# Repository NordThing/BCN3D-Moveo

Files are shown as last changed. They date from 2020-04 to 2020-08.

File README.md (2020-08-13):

## NordThing - What we want to achieve
Make the robotic - and after that try to improve the overall part-list. Now it´s a lot of sourcing of different parts.
It would be nice to minimize the different kind of screws needed.

#What we have modified below this line

Changes:
We have put up a new folder for a Product Breakdown Structure - where it´s easy to see what parts needed and in which phase the project are in right now. This is also possible to modify if we want to 3d print parts or maybe CNC-parts.

#BOM 

Added a file that are changeable and also a progress file for me us as we continue our project

#CAD

We have added a Fusion360 design.

#STL

Put the right orientation of the part to print and also included if support is needed or not.
New parts marked as Nordthing in the end of the files - the original files is still in the folder - with the original name.

Added a picture to ever part that is printed.

## BCN3D MOVEO - ORIGINAL BELOW THIS LINE

This is the repository that contains the CAD files, the STL files, the user manual (with the assembly manual), the firmware, and the Bill of Materials of the BCN3D Moveo.
BCN3D Technologies keeps taking important steps in order to achieve his goal of bringing the digital manufacturing technology to everyone. In this occasion we are presenting the BCN3D Moveo, a robotic arm design from scratch and developed by our engineers in collaboration with the Departament d’Ensenyament from the Generalitat de Catalunya. Its structure is fully printed using additive manufacturing technologies and its electronics are controlled by the software Arduino.
Moveo, fully functional nowadays, has been born, as all the BCN3D Technologies products, with an open and educational wish.

##Why BCN3D Moveo

One of the Departament d’Ensenyament worries is the high price of the materials the grade students must use on their internships. Holding that in mind, an Open Source robotic arm, adaptable by the students and low cost reproducible could take several educational itineraries: mechanical design, automatism, industrial programing, etc.
Thus, the BCN3D Moveo should allow the educational centers to enjoy a modifiable and easily accessible for the students, at a price far lower than the usual industrial equipment they used to have to acquire, with enough output for training purposes.
As a Fundació CIM area, BCN3D Technologies shares its educational vocation. That is the reason why when the Departament d’Ensenyament contacted us in order to suggest and offer this project a year ago we didn’t hesitate on taking that opportunity.
Once we had the robotic arm designed and manufactured we started the last phase of the project, which consisted on an assembling and fine tuning workshop for 15 institutes around Catalonia, which took place in the BCN3D Technologies.
These institutes already have the BCN3D Moveo in their classrooms and workshops, and will have to present an internship program that proves their knowledge about the arm during September.

##Open Source Technology: Github

As we have done with all our developed produtcs, the BCN3D Moveo files will be available for everyone. Thanks to the platform Github, a website where users around the world share their designs, anyone will be able to obtain all the necessary information in order to assemble his own BCN3D Moveo at home.

Unlike the other BCN3D products, the Moveo won’t be commercialized. The project has been born and developed in order to make a move for the community progress starting from the Departament d’Ensenyament idea.
Nevertheless, BCN3D will fee all the Moveo know how on our Github account, as we have been doing with all the BCN3D Technologies products. Thus, the users will be able to find the bill of material (BOM), where all the needed components for the assembling of the arm come detailed, as the CAD designs, so anyone will be able to modify the BCN3D Moveo design as they wish.
Furthermore, the Github users will find the STL files for the structure printing and the assembling, fine tuning and firmware upload manuals, which will be available both in English and Spanish.

## Acknowledgements

This project is based on a project by [Andreas Hölldorfer](http://chaozlabs.blogspot.de/). You can see his original project on [Hackaday.io](https://hackaday.io/project/3800-3d-printable-robot-arm), [Github](https://github.com/4ndreas/BetaBots-Robot-Arm-Project/tree/master), [Youtube](https://www.youtube.com/channel/UCeFKz1UJUd5YuxS1ZikqYwA).

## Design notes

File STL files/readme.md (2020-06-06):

I have uploaded new files with the correct rotation to print the parts. As they are in the original folder you have to rotate them to get them in the right direction.

To print the files you need a print bed with the minimun footprint of 200x200x200mm. If you have this you will be able to print all parts. 

Right now 

Articulation 1 - DONE

Articalation 2 - DONE

Articulation 3 - DONE

Articulation 4 - DONE

Base - DONE

Cover - DONE

Machine Tool - DONE

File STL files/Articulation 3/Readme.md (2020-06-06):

I have uploaded new files with the correct rotation to print the parts. As they are in the original folder you have to rotate them to get them in the right direction.

T3M1C - print time - 25 min - 0.2mm layer height - 20% infill - 0% support - 150mm/sec - PLA - Printed in 101.25 in X and Y to compensate for shrinkage in the plastic.

3M1 - print time - 17h 00 min - 0.2mm layer height - 20% infill - support - 150mm/sec - PLA - Printed in 101.25 in X and Y to compensate for shrinkage in the plastic.

3M2C - print time - 9h 30 min - 0.2mm layer height - 20% infill - support - 250mm/sec - PLA - Printed in 101.25 in X and Y to compensate for shrinkage in the plastic.

3M2 - print time - 8h 0 min - 0.2mm layer height - 20% infill - support - 250mm/sec - PLA - Printed in 101.25 in X and Y to compensate for shrinkage in the plastic.

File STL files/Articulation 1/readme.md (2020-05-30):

I have uploaded new files with the correct rotation to print the parts. As they are in the original folder you have to rotate them to get them in the right direction.

1M1 - print time - 8h 55min - 0.2mm layer height - 20% infill - 100mm/sec - PLA - Printed in 101.25% to compensate for shrinkage in the plastic

1M2 - print time - 12h 05min - 0.2mm layer height - 20% infill - 225mm/sec - PLA - Printed in 101.25% to compensate for shrinkage in the plastic

1M3 - print time - 4h 05min - 0.2mm layer height - 20% infill - 150mm/sec - PLA - Printed in 101.25% to compensate for shrinkage in the plastic

2M1 - print time - 27h 0min - 0.2mm layer height - 20% infill - 150mm/sec - Support - PLA - Printed in 101.25% to compensate for shrinkage in the plastic

Added STL for pulleys and spacer if you want to print instead and don´t have the parts.
This is the files: 

22 -

31 -

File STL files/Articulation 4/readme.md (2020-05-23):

I have uploaded new files with the correct rotation to print the parts. As they are in the original folder you have to rotate them to get them in the right direction.

4M1 - print time - 9h 20 min - 0.2mm layer height - 20% infill - support - 150mm/sec - PLA - Printed in 101.25 in X and Y to compensate for shrinkage in the plastic.

4M2 - print time - 2h 45 min - 0.2mm layer height - 20% infill - 0% support - 150mm/sec - PLA - Printed in 101.25 in X and Y to compensate for shrinkage in the plastic.

4M2C - print time - 3h 40 min - 0.2mm layer height - 20% infill - 0% support - 150mm/sec - PLA  - Printed in 101.25 in X and Y to compensate for shrinkage in the plastic.

T4M1E - print time - 59 min - 0.1mm layer height - 50% infill - support - 150mm/sec - PLA  - Printed in 101.25 in X and Y to compensate for shrinkage in the plastic.

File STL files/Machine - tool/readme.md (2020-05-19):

I have uploaded new files with the correct rotation to print the parts. As they are in the original folder you have to rotate them to get them in the right direction.

Top plate - print time - 47 min - 0.2mm layer height - 20% infill - support - 150mm/sec - PLA - Printed in 101.25 in X and Y to compensate for shrinkage in the plastic.

Bottom plate - print time - 45 min - 0.2mm layer height - 20% infill - support - 150mm/sec - PLA - Printed in 101.25 in X and Y to compensate for shrinkage in the plastic.

Ciliner x 2 - Pivot arm - Servo gear - 1h 20 min - 20%  infill - no support - 100mm/sec - PLA - Printed in 101.25 in X and Y to compensate for shrinkage in the plastic

Gripper left - Gripper right - 1h 47 min -20% infill - support - 150mm/sec - PLA - Printed in 101.25 in X and Y to compensate for shrinkage in the plastic

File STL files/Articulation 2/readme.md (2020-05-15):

I have uploaded new files with the correct rotation to print the parts. As they are in the original folder you have to rotate them to get them in the right direction. Have also put comment here on which of the part that you need to print with support. 

21(22) - print time - 1h 55min - 0.1mm layer height - 50% infill - 150mm/sec - PLA - Printed in 101.25% in X and Y to compensate for shrinkage in the plastic

2M2H - print time - 11h 05min - 0.2mm layer height - 20% infill - 150mm/sec - PLA - Printed in 101.25% in X and Y to compensate for shrinkage in the plastic

2M2M - print time - 11h 00 min - 0.2mm layer height - 20% infill - 150mm/sec - PLA - Printed in 101.25 in X and Y to compensate for shrinkage in the plastic.

T2M1BD - print time - 25 min - 0.2mm layer height - 20% infill - support everywhere - 150mm/sec - PLA - Printed in 101.25 in X and Y to compensate for shrinkage in the plastic.

T2M1BI - print time - 25 min - 0.2mm layer height - 20% infill - support everywhere - 150mm/sec - PLA - Printed in 101.25 in X and Y to compensate for shrinkage in the plastic.

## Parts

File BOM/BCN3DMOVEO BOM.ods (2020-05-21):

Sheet: Components
BOM ID | BOM | QUANTITY | STATUS | COMMENTS
1 | Stepper Motor SM42HT47-1684 1,8º step, 1,6 A, 3600 g·cm 60mm body length | 1 |  | DRV8825 should work
2 | ARDUINO MEGA 2560 | 1
3 | Stepper Driver tb6560 | 6 |  | Do we really need 6pcs TB6560 - ordered 3pcs DRV8825
4 | Power Supply 24V 320W | 1
5 | RAMPS V1.4 | 1
6 | Power converter 24V a 12V | 1
7 | Servo Motor 180§ 55G TORQUE=13KG/CM | 1
8 | Gear Ratio 5:1 Planetary Gearbox Nema 17 Stepper 17HS19-1684S-PG5 ( step 0,35º , 2Nm, 1,68A) | 1
9 | Nema 23, 112mm, Ø8mm flat shaft SM57HT112-3004A, step 1,8º, 3A,28Kg·cm | 2 |  | 2pcs TB6560
10 | Stepper Motor SM35HT36-1004A, 1,8º step, 1A, 1400g·cm | 1
11 | Stepper Motor nema 17 SM42HT33-1334, 1,8º step, 1,33A, 2200 g·cm | 1
12 | Chrome steel smooth bar-134mm | 1
13 | Chrome steel smooth bar-114mm | 1
14 | Chrome steel smooth bar-80mm | 1
15 | Ball Bearing 608ZZ 8mm x 22mm x 7mm | 10
16 | Ball Bearing 625ZZ 5mm x 16mm x 5mm | 8 |  |  | https://uk.misumi-ec.com/vona2/detail/221000531116/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
17 | Ball Bearing 624ZZ 4mm x 13mm x 5mm | 9 |  |  | https://uk.misumi-ec.com/vona2/detail/221000531116/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
18 | Ball Bearing 623ZZ 3mm x 10mm x 4mm | 3 |  |  | https://uk.misumi-ec.com/vona2/detail/221000531116/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
19 | Brass insert M4 | 3 |  |  | https://uk.misumi-ec.com/vona2/detail/221000748262/
20 | Brass insert M3 | 20 |  |  | https://uk.misumi-ec.com/vona2/detail/221000748262/
21 | Pulley T5, Bore 8mm, 14 tooth, 17mm width | 3 |  | Also available as STL to print instead named 21-NordThing
22 | Pulley T5, Bore 5mm, 10 tooth, 17 mm width | 2 |  | Also available as STL to print instead named 22-NordThing | Printing 50%infill 0.1mm layer height
23 | ROD BAR M8 L 42mm | 1
24 | ZCOUPLING STEEL 5 TO 8 mm rigid | 1
25 | Axial Fan DC 24V 80x80mm | 1
26 | Axial Fan DC 24V 50x50mm | 1
27 | Powwer supply cable IEC 1,8m | 1
28 | Cable USB 2.0 AM/BM 1,8m | 1
29 | Cable Ties | 10
30 | Selfoil bearing 5mm x 8mm x 10mm | 8
31 | Selfoil bearing 8mm x 12mm x 20mm | 2 |  | Also available as STL to print instead named 31-NordThing
32 | Wood Base - 550mm x 550mm x 16mm | 1
33 | Breco belt T5, 16mm width, L 180cm | 1.8 |  | 2pc 36cm belt

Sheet: Fasteners
BOM ID | BOM | QUANTITY | STATUS | COMMENT
101 | Dimension A: M-3 Dimension B: 8 mm | 4
102 | Dimension A: M-3 Dimension B: 10 mm | 30
103 | Dimension A: M-3 Dimension B: 12 mm | 6
104 | Dimension A: M-3 Dimension B: 16 mm | 13
105 | Dimension A: M-3 Dimension B: 20 mm | 4
106 | Dimension A: M-3 Dimension B: 25 mm | 5
107 | Dimension A: M-3 Dimension B: 30 mm | 2
108 | Dimension A: M-3 Dimension B: 35 mm | 4
109 | Dimension A: M-3 Dimension B: 40 mm | 7
110 | Dimension A: M-4 Dimension B: 10 mm | 2
111 | Dimension A: M-4 Dimension B: 12 mm | 2
112 | Dimension A: M-4 Dimension B: 16 mm | 8
113 | Dimension A: M-4 Dimension B: 20 mm | 3
114 | Dimension A: M-4 Dimension B: 25 mm | 4
115 | Dimension A: M-4 Dimension B: 30 mm | 8
116 | Dimension A: M-4 Dimension B: 40 mm | 4
117 | Dimension A: M-4 Dimension B: 45 mm | 6
118 | Dimension A: M-4 Dimension B: 60 mm | 4
119 | Dimension A: M-5 Dimension B: 14 mm | 120
120 | Dimension A: M-5 Dimension B: 20 mm | 8
121 | Dimension A: M-8 Dimension B: 65 mm | 1
122 | Dimension A: M-3 Nut | 30
123 | Dimension A: M-4 Nut | 4
124 | Dimension A: M-4 Locknut | 18
125 | Dimension A: M-5 Locknut | 16
126 | Dimension A: M-8 Locknut | 2
127 | Washer M-3 | 10

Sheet: Printed parts
BOM ID | PARTS | NAME | QUANTITY | STATUS | COMMENT
201 | Articulation 1 | 1M1 | 1
202 |  | 1M2 | 1
203 |  | 1M3 | 1
204 | Articulation 2 | 2M1 | 1
205 |  | 2M2M | 1
206 |  | 2M2H | 1
207 |  | T2M1D | 1
208 |  | T2M1I | 1
209 | Articulation 3 | 3M1 | 1
210 |  | 3M2C | 1
211 |  | 3M2 | 1
212 |  | T3M1 | 1
213 | Articulation 4 | 4M1 | 1
214 |  | 4M2 | 1
215 |  | 4M2C | 1
216 |  | T4M1 | 1
217 | Machine - tool | Top plate | 1
218 |  | Bottom plate | 1
219 |  | Cilinder | 2
220 |  | Pivot arm | 1
221 |  | Gripper left | 1
222 |  | Gripper right | 1
223 |  | Idol gear | 1
224 |  | Servo gear | 1
225 | Box electronics | Box | 1
226 |  | Fan module | 1
227 |  | Suport Drivers | 1
228 | Base | Potes | 4
229 | Cover | Tapa 2M1 | 2
230 |  | Tapa 3M1 | 2
231 |  | Tapa 4M1 | 2
232 |  | Tapa TBB | 1

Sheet: Module 1
BOM ID | BOM | QUANTITY | STATUS | COMMENTS
120 | Dimension A: M-5 Dimension B: 20 mm | 8
16 | Ball Bearing 625ZZ 5mm x 16mm x 5mm | 8
30 | Selfoil bearing 5mm x 8mm x 10mm | 8
125 | Dimension A: M-5 Locknut | 8
15 | Ball Bearing 608ZZ 8mm x 22mm x 7mm | 2
202 | 1M2 | 1
121 | Dimension A: M-8 Dimension B: 65 mm | 1
124 | Dimension A: M-4 Locknut | 6
31 | Selfoil bearing 8mm x 12mm x 20mm | 1
201 | 1M1 | 1
203 | 1M3 | 1
1 | Stepper Motor SM42HT47-1684 1,8º step, 1,6 A, 3600 g·cm 60mm body length | 1
101 | Dimension A: M-3 Dimension B: 8 mm | 4
22 | Pulley T5, Bore 5mm, 10 tooth, 17 mm width | 1

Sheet: Module 2
BOM ID | BOM | QUANTITY | STATUS | COMMENTS
123 | Dimension A: M-4 Nut | 2
124 | Dimension A: M-4 Locknut | 4
206 | 2M2H | 1
123 | Dimension A: M-4 Nut | 2
116 | Dimension A: M-4 Dimension B: 40 mm | 4
205 | 2M2M | 1
207 | T2M1D | 1
113 | Dimension A: M-4 Dimension B: 20 mm | 1
123 | Dimension A: M-4 Nut | 1
122 | Dimension A: M-3 Nut | 1
17 | Ball Bearing 624ZZ 4mm x 13mm x 5mm | 3
208 | T2M1I | 1
113 | Dimension A: M-4 Dimension B: 20 mm | 1
123 | Dimension A: M-4 Nut | 1
122 | Dimension A: M-3 Nut | 1
17 | Ball Bearing 624ZZ 4mm x 13mm x 5mm | 3
204 | 2M1 | 1
106 | Dimension A: M-3 Dimension B: 25 mm | 2
9 | Nema 23, 112mm, Ø8mm flat shaft SM57HT112-3004A, step 1,8º, 3A,28Kg·cm | 2
119 | Dimension A: M-5 Dimension B: 14 mm | 8
125 | Dimension A: M-5 Locknut | 8
21 | Pulley T5, Bore 8mm, 14 tooth, 17mm width | 2
15 | Ball Bearing 608ZZ 8mm x 22mm x 7mm | 2
12 | Chrome steel smooth bar-134mm | 1
19 | Brass insert M4 | 2
20 | Brass insert M3 | 2
102 | Dimension A: M-3 Dimension B: 10 mm | 6
229 | Tapa 2M1 | 1

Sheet: Tool assembly
BOM ID | BOM | QUANTITY | STATUS | COMMENTS
217 | Top plate
104 | Dimension A: M-3 Dimension B: 16 mm
102 | Dimension A: M-3 Dimension B: 10 mm
219 | Cilinder
127 | Washer M-3
224 | Servo gear
223 | Idol gear
220 | Pivot arm
127 | Washer M-3
218 | Bottom plate
122 | Dimension A: M-3 Nut
221 | Gripper left
222 | Gripper right
104 | Dimension A: M-3 Dimension B: 16 mm
122 | Dimension A: M-3 Nut

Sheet: Module 3 STEP I
BOM ID | BOM | QUANTITY | STATUS | COMMENTS
209 | 3M1
112 | Dimension A: M-4 Dimension B: 16 mm
212 | T3M1
17 | Ball Bearing 624ZZ 4mm x 13mm x 5mm
113 | Dimension A: M-4 Dimension B: 20 mm
123 | Dimension A: M-4 Nut
109 | Dimension A: M-3 Dimension B: 40 mm
122 | Dimension A: M-3 Nut
210 | 3M2C
11 | Stepper Motor nema 17 SM42HT33-1334, 1,8º step, 1,33A, 2200 g·cm
102 | Dimension A: M-3 Dimension B: 10 mm
24 | ZCOUPLING STEEL 5 TO 8 mm rigid
23 | ROD BAR M8 L 42mm
15 | Ball Bearing 608ZZ 8mm x 22mm x 7mm

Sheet: Module 4
BOM ID | BOM | QUANTITY | STATUS | COMMENTS
213 | 4M1
15 | Ball Bearing 608ZZ 8mm x 22mm x 7mm
126 | Dimension A: M-8 Locknut
20 | Brass insert M3
232 | Tapa TBB
103 | Dimension A: M-3 Dimension B: 12 mm
216 | T4M1
18 | Ball Bearing 623ZZ 3mm x 10mm x 4mm
122 | Dimension A: M-3 Nut
105 | Dimension A: M-3 Dimension B: 20 mm
122 | Dimension A: M-3 Nut
107 | Dimension A: M-3 Dimension B: 30 mm
15 | Ball Bearing 608ZZ 8mm x 22mm x 7mm
214 | 4M2
215 | 4M2C
122 | Dimension A: M-3 Nut
114 | Dimension A: M-4 Dimension B: 25 mm
124 | Dimension A: M-4 Locknut
14 | Chrome steel smooth bar-80mm
10 | Stepper Motor SM35HT36-1004A, 1,8º step, 1A, 1400g·cm
22 | Pulley T5, Bore 5mm, 10 tooth, 17 mm width
101 | Dimension A: M-3 Dimension B: 8 mm
20 | Brass insert M3
231 | Tapa 4M1
103 | Dimension A: M-3 Dimension B: 12 mm
104 | Dimension A: M-3 Dimension B: 16 mm
7 | Servo Motor 180§ 55G TORQUE=13KG/CM
102 | Dimension A: M-3 Dimension B: 10 mm

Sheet: Module 3 STEP II
BOM ID | BOM | QUANTITY | STATUS | COMMENTS
104 | Dimension A: M-3 Dimension B: 16 mm
109 | Dimension A: M-3 Dimension B: 40 mm
122 | Dimension A: M-3 Nut
211 | 3M2
15 | Ball Bearing 608ZZ 8mm x 22mm x 7mm
13 | Chrome steel smooth bar-114mm
8 | Gear Ratio 5:1 Planetary Gearbox Nema 17 Stepper 17HS19-1684S-PG5 ( step 0,35º , 2Nm, 1,68A)
21 | Pulley T5, Bore 8mm, 14 tooth, 17mm width
122 | Dimension A: M-3 Nut
230 | Tapa 3M1
102 | Dimension A: M-3 Dimension B: 10 mm

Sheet: Base Assembly
BOM ID | BOM | QUANTITY | STATUS | COMMENTS
32 | Wood Base - 550mm x 550mm x 16mm
116 | Dimension A: M-4 Dimension B: 40 mm
124 | Dimension A: M-4 Locknut
117 | Dimension A: M-4 Dimension B: 45 mm
121 | Dimension A: M-8 Dimension B: 65 mm
126 | Dimension A: M-8 Locknut
124 | Dimension A: M-4 Locknut
115 | Dimension A: M-4 Dimension B: 30 mm
225 | Box
227 | Suport Drivers
226 | Fan module
108 | Dimension A: M-3 Dimension B: 35 mm
115 | Dimension A: M-4 Dimension B: 30 mm

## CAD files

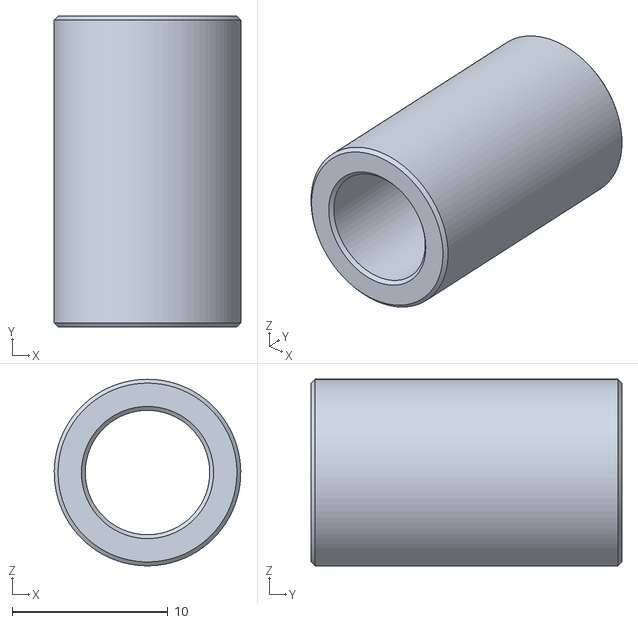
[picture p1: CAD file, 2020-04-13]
STL files/Articulation 1/31-NordThing.stl
12.0 x 20.0 x 12.0

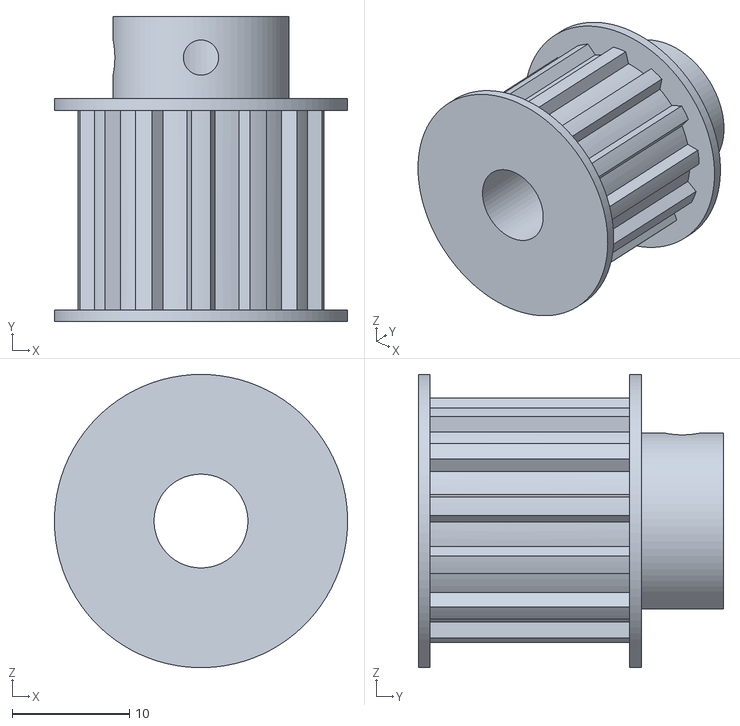
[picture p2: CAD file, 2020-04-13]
STL files/Articulation 2/21-NordThing.stl
25.0 x 26.0 x 25.0

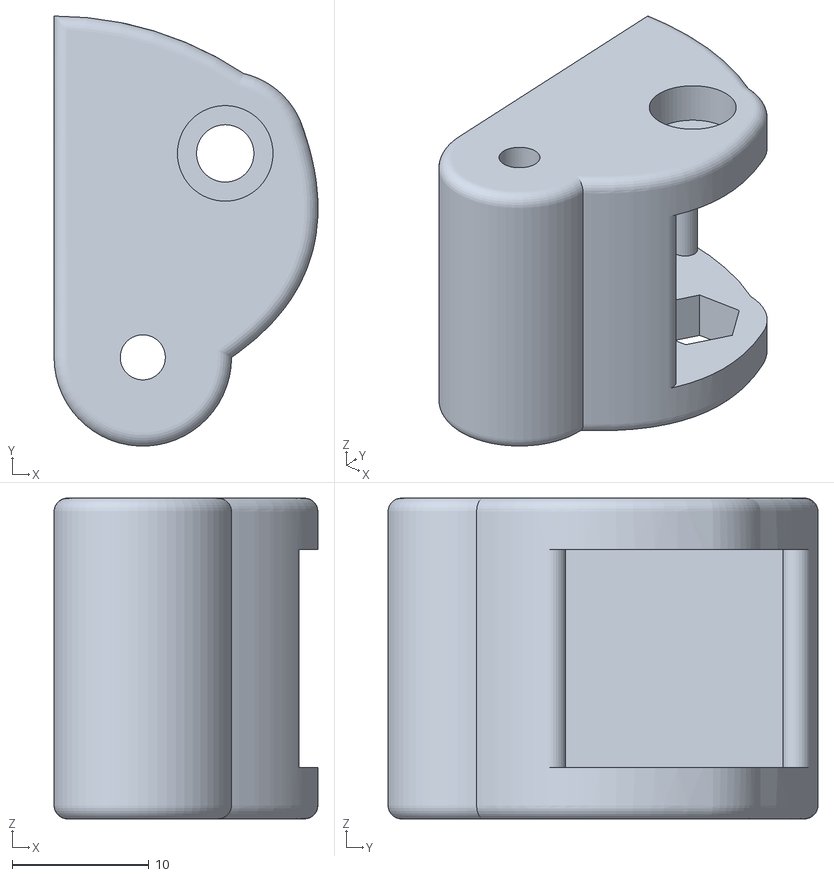
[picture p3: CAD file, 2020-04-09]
STL files/Articulation 3/T3M1C-NordThing.stl
19.3 x 31.5 x 23.5

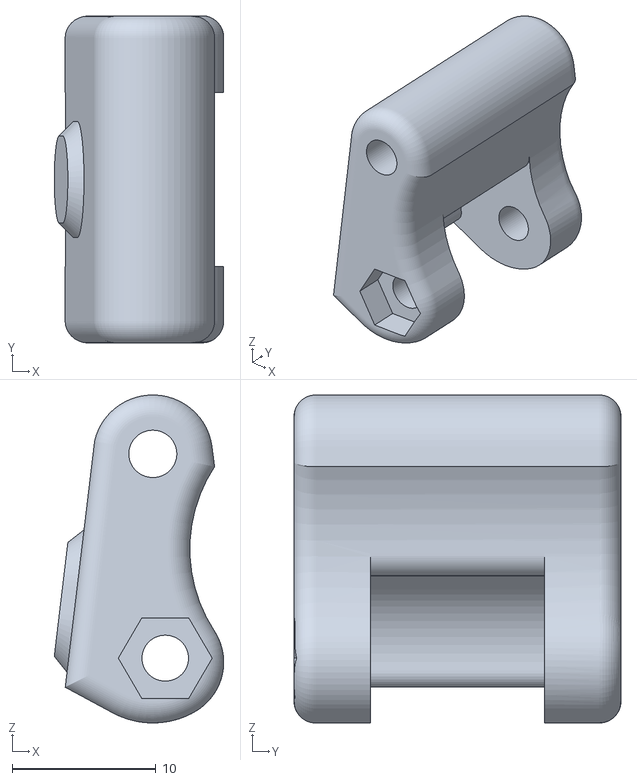
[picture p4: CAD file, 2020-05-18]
STL files/Articulation 4/T4M1E-NordThing.stl
11.8 x 22.8 x 22.9

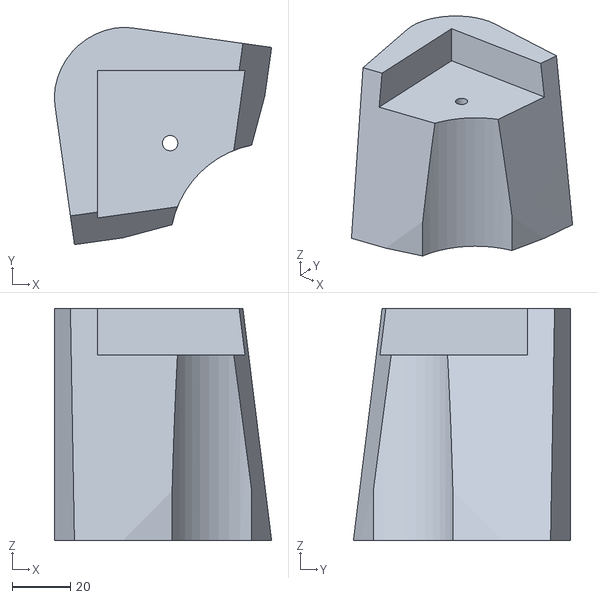
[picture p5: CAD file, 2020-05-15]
STL files/Base/Potes-NordThing.stl
74.9 x 74.9 x 80.0

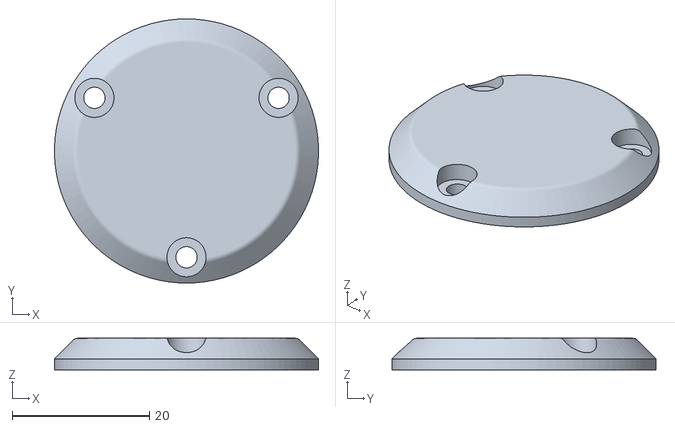
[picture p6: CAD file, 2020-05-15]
STL files/Cover/Tapa 4M1-NordThing.stl
38.5 x 38.5 x 4.60

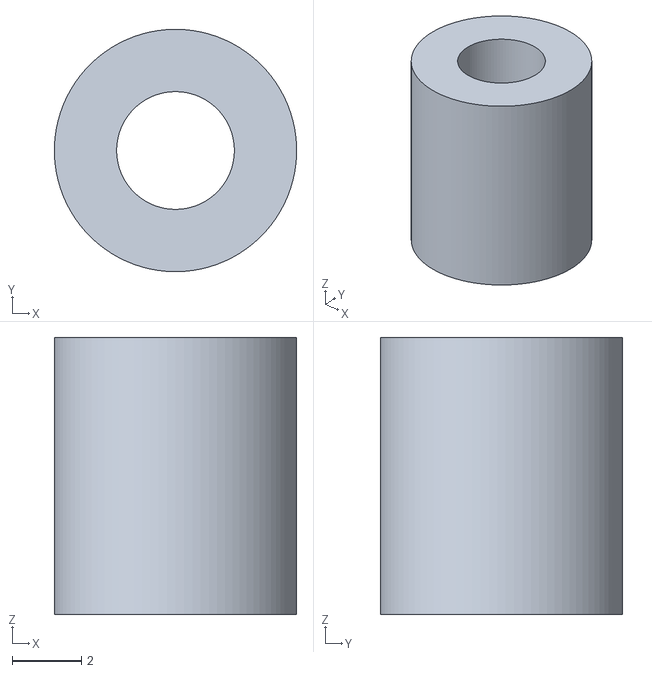
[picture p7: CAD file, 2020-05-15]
STL files/Machine - tool/Cilinder-NordThing.stl
7.00 x 7.00 x 8.00

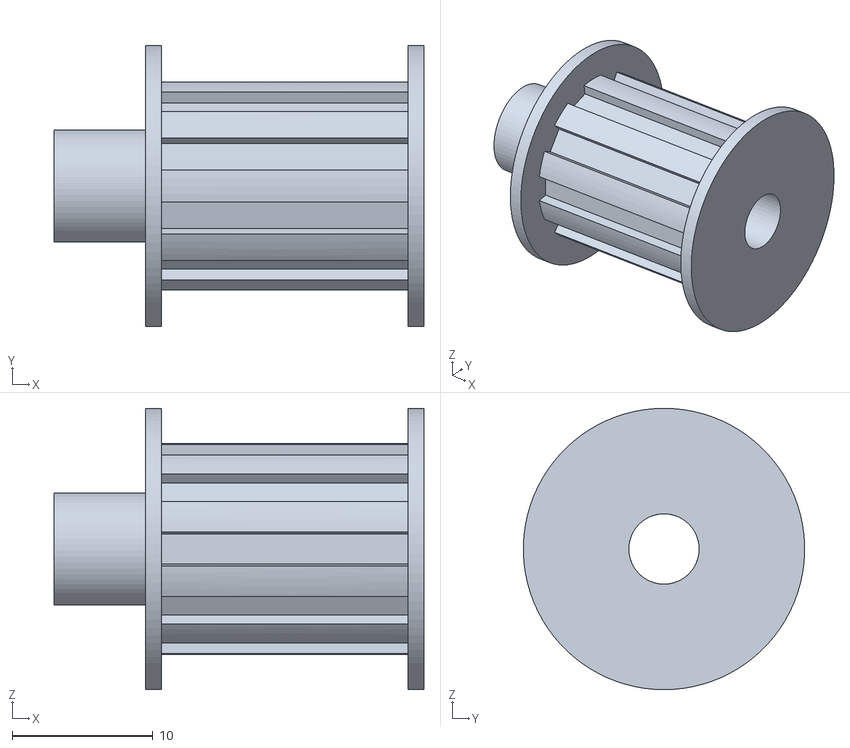
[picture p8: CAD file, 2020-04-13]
STL files/Articulation 1/22-NordThing.stl
26.3 x 20.0 x 20.0

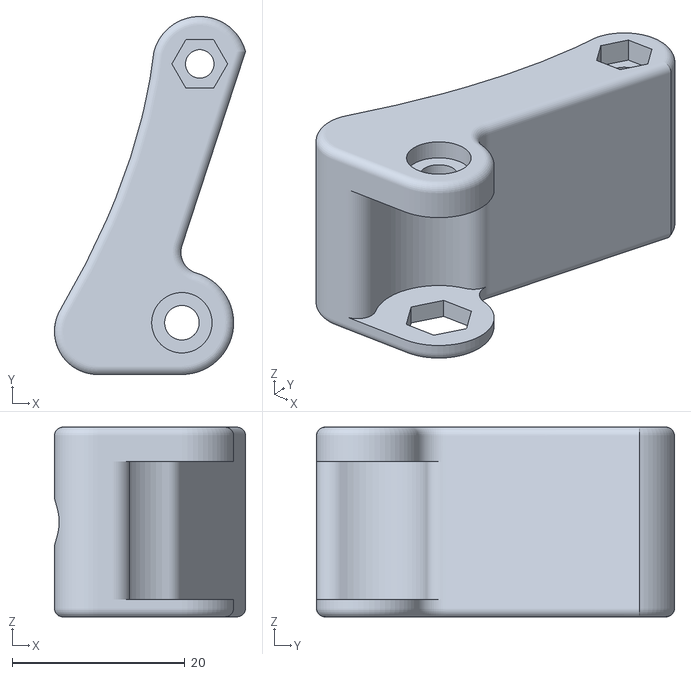
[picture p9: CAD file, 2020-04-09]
STL files/Articulation 2/T2M1BI-NordThing.stl
22.2 x 41.5 x 22.0

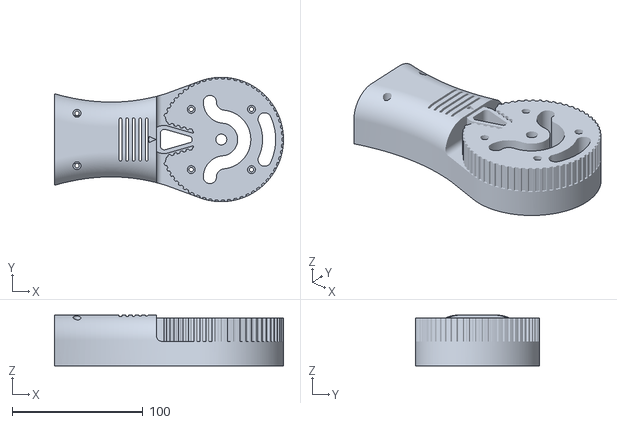
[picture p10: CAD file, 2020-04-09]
STL files/Articulation 3/3M2C-NordThing.stl
175.0 x 95.0 x 38.8

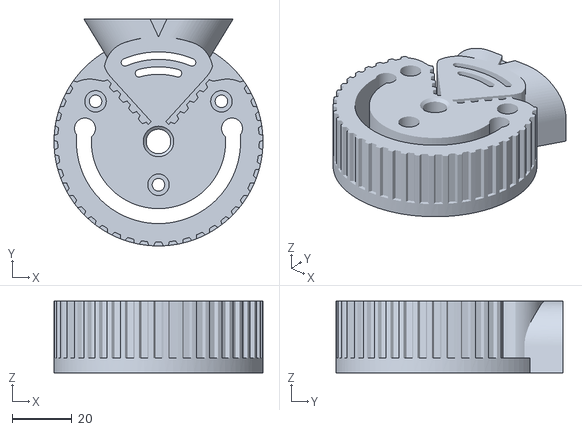
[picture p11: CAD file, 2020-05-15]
STL files/Articulation 4/4M2C-NordThing.stl
70.0 x 76.0 x 24.0

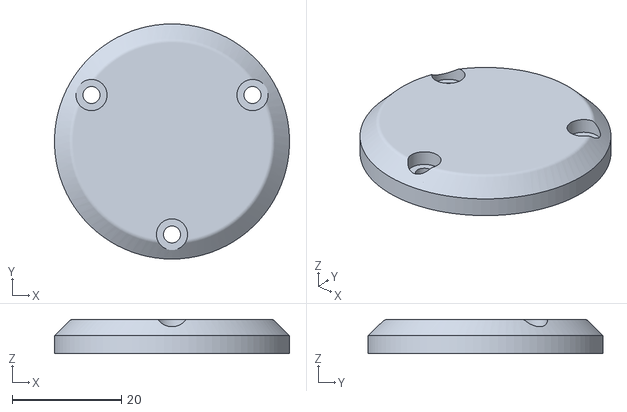
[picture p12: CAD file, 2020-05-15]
STL files/Cover/Tapa 3M1-NordThing.stl
43.0 x 43.0 x 6.30

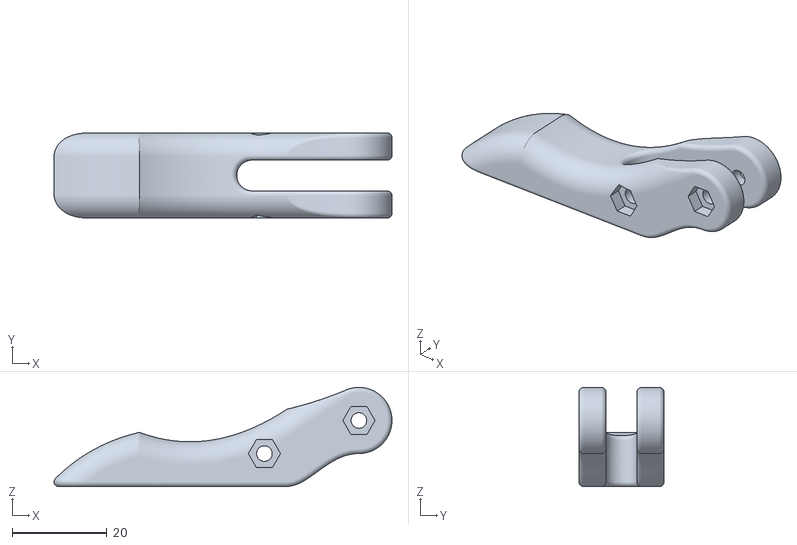
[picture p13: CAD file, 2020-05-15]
STL files/Machine - tool/Gripper Left-NordThing.stl
71.5 x 18.0 x 21.0

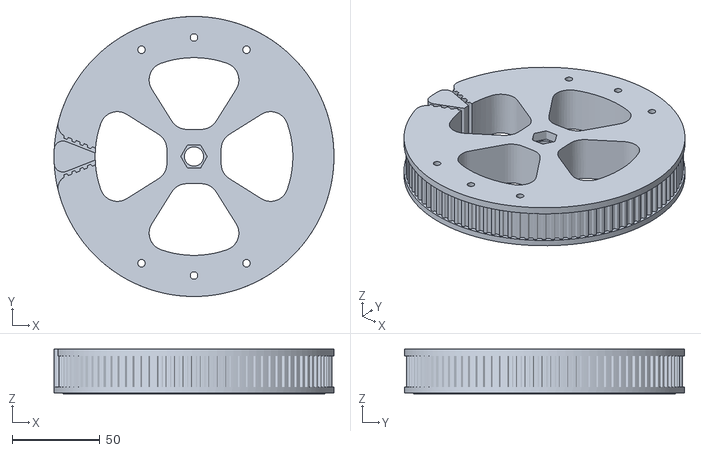
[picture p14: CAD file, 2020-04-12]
STL files/Articulation 1/1M1-NordThing.stl
160.0 x 160.0 x 25.5

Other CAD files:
STL files/Articulation 2/T2M1BD-NordThing.stl
STL files/Articulation 3/3M2-NordThing.stl
STL files/Articulation 4/4M2-NordThing.stl
STL files/Cover/Tapa TBB-NordThing.stl
STL files/Articulation 1/1M2-NordThing.stl
STL files/Articulation 2/2M2H-NordThing.stl
STL files/Articulation 2/2M2M-NordThing.stl
STL files/Articulation 3/3M1-NordThing.stl
STL files/Cover/Tapa 2M1-NordThing.stl
STL files/Machine - tool/Bottom Plate-NordThing.stl
STL files/Machine - tool/Gripper Right-NordThing.stl
STL files/Machine - tool/Idol Gear-NordThing.stl
STL files/Machine - tool/Pivot Arm-NordThing.stl
STL files/Machine - tool/Servo Gear-NordThing.stl
STL files/Machine - tool/Top Plate-NordThing.stl

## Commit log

2020-02-29 Added Fusion360 complete assembly
    This is assembled in Fusion360
2020-04-12 Add files via upload
    Added the newest file - the last one didn´t have the arrow.
    [1M1-NordThing.stl]
2020-04-13 Delete 21-NordThing.stl
    Wrong name..
    [21-NordThing.stl]
2020-05-21 Recreate the BOM in a format that are changeable
    [BCN3DMOVEO BOM.ods]
